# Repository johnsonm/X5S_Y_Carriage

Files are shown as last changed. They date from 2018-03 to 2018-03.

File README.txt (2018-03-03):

                   .:                     :,                                          
,:::::::: ::`      :::                   :::                                          
,:::::::: ::`      :::                   :::                                          
.,,:::,,, ::`.:,   ... .. .:,     .:. ..`... ..`   ..   .:,    .. ::  .::,     .:,`   
   ,::    :::::::  ::, :::::::  `:::::::.,:: :::  ::: .::::::  ::::: ::::::  .::::::  
   ,::    :::::::: ::, :::::::: ::::::::.,:: :::  ::: :::,:::, ::::: ::::::, :::::::: 
   ,::    :::  ::: ::, :::  :::`::.  :::.,::  ::,`::`:::   ::: :::  `::,`   :::   ::: 
   ,::    ::.  ::: ::, ::`  :::.::    ::.,::  :::::: ::::::::: ::`   :::::: ::::::::: 
   ,::    ::.  ::: ::, ::`  :::.::    ::.,::  .::::: ::::::::: ::`    ::::::::::::::: 
   ,::    ::.  ::: ::, ::`  ::: ::: `:::.,::   ::::  :::`  ,,, ::`  .::  :::.::.  ,,, 
   ,::    ::.  ::: ::, ::`  ::: ::::::::.,::   ::::   :::::::` ::`   ::::::: :::::::. 
   ,::    ::.  ::: ::, ::`  :::  :::::::`,::    ::.    :::::`  ::`   ::::::   :::::.  
                                ::,  ,::                               ``             
                                ::::::::                                              
                                 ::::::                                               
                                  `,,`

https://www.thingiverse.com/thing:2580773
TronXY X5S - upgraded parts for Gantry and Belt Idlers by 3DFreezeMe is licensed under the Creative Commons - Attribution - Non-Commercial - Share Alike license.
http://creativecommons.org/licenses/by-nc-sa/3.0/

# Summary

For the TronXY X5S I have designed some upgrade parts. Mainly to improve the gantry which uses Acrylic parts which flex and break easily, the stock idlers and belt path.

See short video clip:
https://youtu.be/3yFbaJzWN30
<br>
The stock belt path is nowhere near parallel and perpendicular where needed, so I designed custom Corner Idler Plates. Added ridges and counter sunk extrusion cur outs to make it more sturdy.

The four wheeled Y carriages have basically one wheel too many, three make a plane. During movement I could see wheels not turning at all due to the forces on the plates. The 3 Wheeler solves that as well. Added ridges and counter sunk extrusion cur outs to make it more sturdy.
<br>
_____
[EDIT 1]
If you want to use eccentric nuts for the outer wheels, see the great remix that Joar shared:
https://www.thingiverse.com/thing:2599479
_____
<br>
_Parts included and needed:_

_Printed parts_ (I printed them at 0.28 layer height, 4 top/bottom/perimeters with 80% full Honeycomb Infill):

- 2x X5S_Y-carriage_3w_ridged_spacers.stl ('3 Wheeler edition' with ridges and integrated wheel spacers)
- 1x Corner_Idlers_Plate.stl ('as is' for Front Left side)
- 1x Corner_Idlers_Plate_mirrored.stl (mirrored in XY for Front Right side)
- 8x M5_holder_608_bearing.stl (when you gonna use them as idlers)
- 8x 608_bearing_sleeve.stl (when you gonna use them as idlers)
<br>
The following files you can download at SgaboLab, the designer of them. Check out his other great upgrades for the X5S as well!:
https://www.thingiverse.com/thing:2574935/#files
<br>
- 2x spacer A1-spessore-cuscinetto-cinghie-carrelli-8e4mm.stl (under high idlers on Y carriage)
- 2x spacer C-spessore-torri-cuscinetto-20x8e4.stl (under high idlers on Corner Idler Plates, print them 1mm lowered in Z height --> 7mm high)
- 1x B2-staffa-cart-estrusore-V2.stl (for X Carriage belt riser)
- 3x B1-spessore-ruote-ext-6mm.stl (for X Carriage Wheels)
<br>

_Hardware needed:_

- 8x 608zz bearing (if you do not have 'official idlers' planned already and you gonna use them as idlers)
- 4x M5x50 screws
- 3x M5x40 screws
- 1x M5x35 screws (re-use from kit)
- 2x M5x30 screws (re-use from kit)
- 10x M5 washers medium size
- 12x M5 washers small size (re-use from kit)
- 4x M4x16 screws
- 4x M4x9 screws (re-use from kit)
- 8x M4 washers medium size
- 12x M4 washers small size (re-use from kit)
- 8x T-nuts (re-use from kit)
<br>

_Instructions and parts used:_

Y-Carriage:

For assembling the mirrored right side corner idler plate, use your free side cutters to snip off part of the outside ridge where the end stop plate is mounted to make it fit. See photo.

Front Left corner idler plate:
- high idler: M5x50 screwed into frame,  
- low idler: use the M5x25 from the frame

Front Right corner idler plate:
- high idler: use a M5x40 (the M5x35 from stock wheel setup is just too short) 
- low idler: M5x50 screwed into frame

Use M4x16 with M4 medium washers and the hammer nuts to mount the plates to the extrusion. 
<br>
For instructions to assemble the belt riser bracket and X carriage spacers under the wheels, check the Thingy of SgabLab who deisgned them here:
https://www.thingiverse.com/thing:2574935
<br>
_Also, check out some of my other add-on things for the TronXY X5S printer:_
https://www.thingiverse.com/thing:2565565
https://www.thingiverse.com/thing:2573443

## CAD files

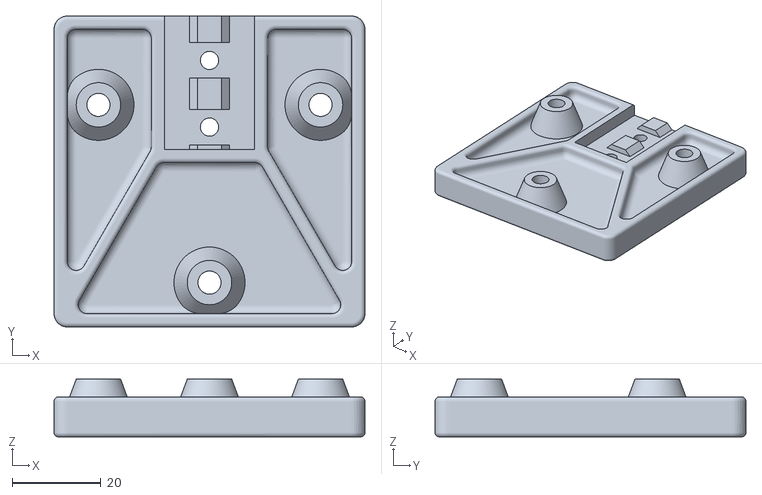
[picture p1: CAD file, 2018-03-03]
y-carriage.stl
70.0 x 70.0 x 13.0

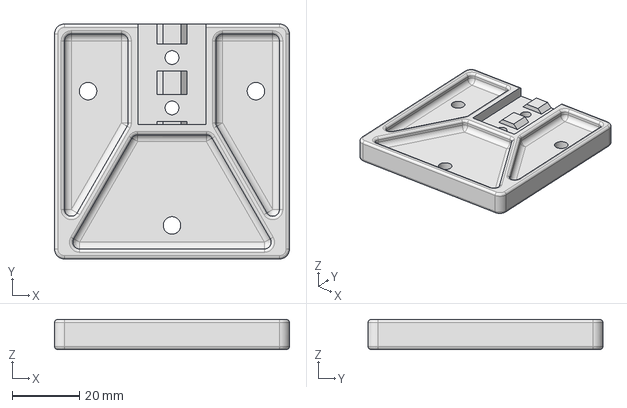
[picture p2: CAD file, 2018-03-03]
X5S_Y-carriage_3w_ridged.iges
70.0 x 70.0 x 9.00 mm

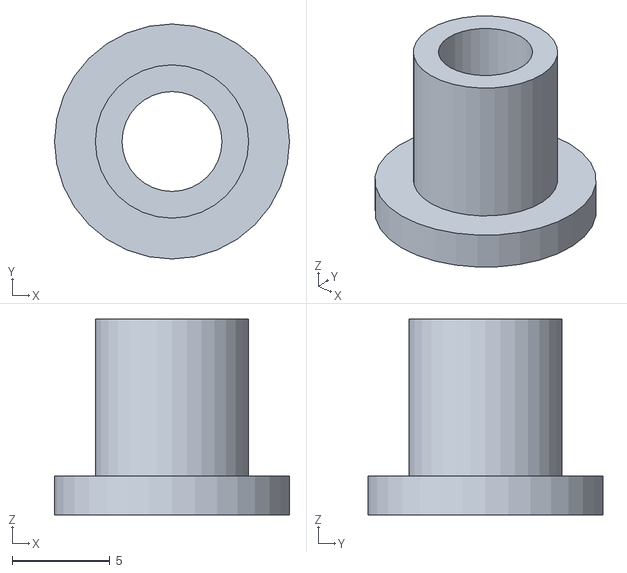
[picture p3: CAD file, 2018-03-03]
M5_holder_608_bearing.stl
12.0 x 12.0 x 10.0

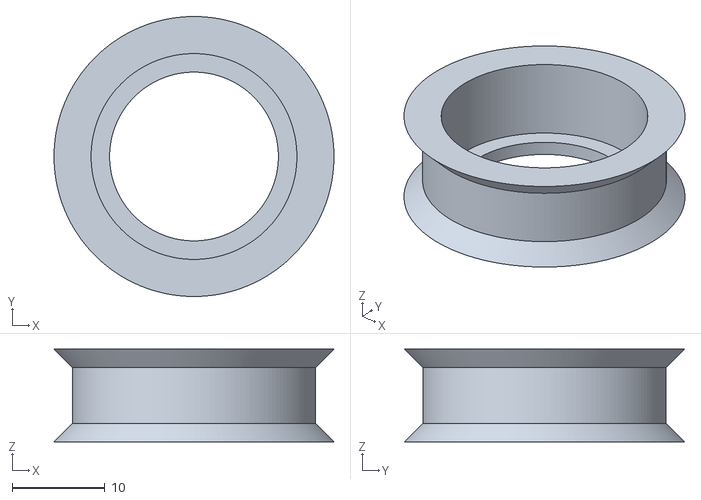
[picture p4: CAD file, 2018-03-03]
608_bearing_sleeve.stl
30.2 x 30.2 x 10.0

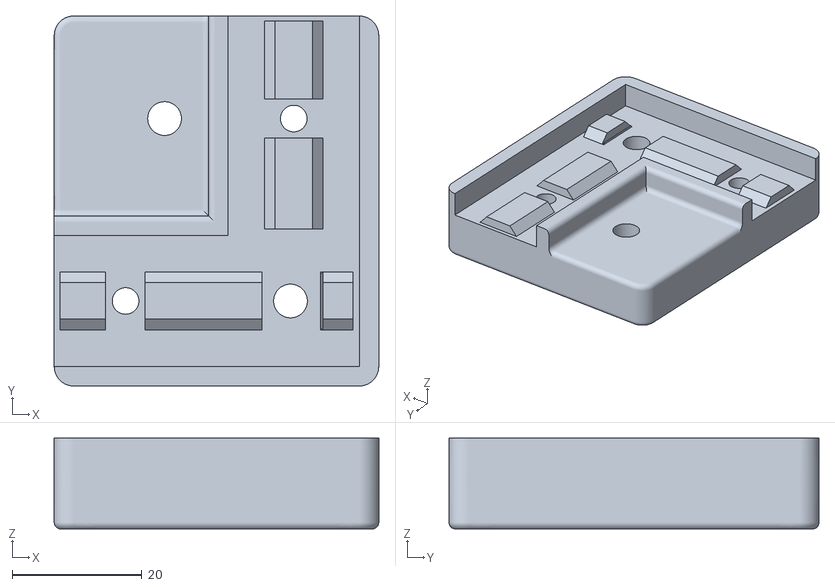
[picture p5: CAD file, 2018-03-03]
Corner_Idlers_Plate.stl
50.0 x 57.0 x 14.0

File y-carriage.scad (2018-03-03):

x1 = 12;
x2 = 37;
x3 = 62;
y1 = -22;
y2 = -62;
z = 5;
s_h = 8;
d = 5.2;
r1 = 8;
r2 = 5;

module crosshair(x, y, z, d) {
    // Used to locate centers and size holes
    translate([x, y, 0]) union() {
        translate([-d/2, -0.1, 0]) cube([d, 0.2, z]);
        translate([-0.1, -d/2, 0]) cube([0.2, d, z]);
    }
}
module support(x, y) {
    $fn=60;
    // this holds the wheel
    translate([x, y, 0]) difference() {
        translate([0, 0, z-0.01]) cylinder(r1=r1, r2=r2, h=s_h+0.01);
        cylinder(d=d, h=z+s_h+0.01);
    }
}

module carriage() {
    import("X5S_Y-carriage_3w_ridged.stl"); // FreeCAD exported from .iges
    support(x1, y1);
    support(x2, y2);
    support(x3, y1);
    //crosshair(12, -22, 5, 5);
    //crosshair(62, -22, 5, 5);
    //crosshair(37, -62, 5, 5);
}
carriage();

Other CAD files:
X5S_Y-carriage_3w_ridged_spacers.stl
Corner_Idlers_Plate_mirrored.stl
X5S_Y-carriage_3w_ridged.stl

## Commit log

2018-03-03 Copy of https://www.thingiverse.com/thing:2580773
    [608_bearing_sleeve.stl, Corner_Idlers_Plate.stl, Corner_Idlers_Plate_mirrored.stl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]
2018-03-03 Re-build Y carriage for slic3r
    Cura is able to slice the original Y carriage, but both slic3r and slic3r-PE
    fail to see it as a manifold. I used FreeCAD to convert the iges file to
    an stl, and then used OpenSCAD to import the stl and add the spacers back to
    it, and now both slic3r variants can slice it. I sliced it with slic3r-PE
    to print on the X5S with PLAPro/PLA+ and have included that gcode.
    [y-carriage.scad, y-carriage.stl]
